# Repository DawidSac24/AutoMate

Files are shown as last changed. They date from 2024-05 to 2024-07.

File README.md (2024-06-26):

# AutoMate



> © INRACI


## Video 

https://github.com/DawidSac24/AutoMate/assets/171250080/86d8ad7e-6ad9-42c3-80ba-5ba671484344

## Summary

- [Project source](#Project-source)
- [Introduction](#Introduction)
- [The block diagram](#The-block-diagram) 
- [Characteristics](#Characteristics)
- [Used libraries](#Used-libraries)
- [My code](#My-code)
- [The principle diagrams](#The-principle-diagrams)
  - [The principle diagram without connector](#The-principle-diagram-without-connector)
  - [The principle diagram with connector](#The-principle-diagram-with-connector)
- [The PCB](#The-PCB) 
- [Parts list](#Parts-list) 
  - [XY table](#XY-table)
  - [Transmission](#Transmission)
  - [Electronics](#Electronics)
  - [Box](#Box)
  - [Bolting](#Bolting)

## Project source
I would like to sincerely thank the author of the site from which I drew inspiration :
[instructables.com/Automated-Chessboard](https://www.instructables.com/Automated-Chessboard/)

## Introduction
I am pleased to present my exciting project: Auto-Mate, an automated chess game designed to give a new dimension to this game. By enabling remote movement of pieces, I create the possibility of bringing chess online or against a robot on a chessboard. To achieve this, I have developed a case that handles the movement of the pieces. Auto-Mate is equipped with a screen, allowing for the automatic movement of pieces. It is also possible to move them manually using sensors located beneath the board. I made this project because I enjoy playing chess. It has allowed me to learn many new things in electronics and programming. Auto-mate is still in developpement (mostly the code). I invite you to see my work in the [TFE](TFE) folder, there is a more detailed documentation of my project. I also want to add that I am still a young student. My work and my code are far from perfect and contain many errors. My goal, above all, is to present my work and maybe inspire some people.

## The block diagram

Schema bloc

#### The Microcontroller
It is the brain of the setup, allowing control of each component (motors, motor drivers, electromagnet, multiplexers, and touchscreen) and reading the necessary data (limit switches, buttons, magnetic sensors, and touchscreen).
#### The Touchscreen
It provides the ability to navigate through menus to change the AI difficulty, display the timer, modify game settings, or select the game mode. It communicates with the UART, an asynchronous serial bus.
#### Motor Drivers A and B
They control the coils of the stepper motors and provide the necessary current to operate them.
#### Motors A and B
They are connected to a belt system, moving the electromagnet on the x and y axes.
#### The Electromagnet
It is placed underneath the board and is used to move the magnetized pieces on the board.
#### The Multiplexer
It successively reads the signals from the 8 sensors and sends the data to the microprocessor.
#### Magnetic Sensors
They determine the presence of the chess pieces.
#### x and y Limit Switches
They locate the position of the electromagnet by resetting at the start of the game. They allow for calibration of its position and help avoid potential misalignments during movement.

## Characteristics
### General :
- Color graphical resistive touchscreen, 320×240 pixels
- 2 arcade buttons
- 32 magnetized pieces
- Operating modes: 1/2 players
- Automatic piece movement
- Automatic piece detection
- Area for eliminated pieces
### Electronics :
- Power supply: 12V, 2A
### Mechanics :
- Dimensions: 496 mm x 496 mm x 100 mm
- 6 plywood faces
- Weight: 4 kg

## Used libraries
I planned to use a [Nextion library](https://docs.arduino.cc/learn/built-in-libraries/software-serial/) for the code of my touchscreen, but I accidentally connected my screen to the wrong pins of my microcontroller and had to use my touchscreen manually with the [SoftwareSerial library](https://docs.arduino.cc/learn/built-in-libraries/software-serial/).

## My code
I wanted to add an algorithm that would be used for an enemy robot. Unfortunately, I did not finish verifying the allowed moves for the pawns, which is required for the algorithm. If you would like to see my algorithm development then, you would have to wait for the next updates. To compensate, here is what I plan to do for the enemy robot algorithm:
obraz_2024-06-16_125101164

It is called the Min-Max algorithm, and I will use Alpha-Beta pruning, which evaluates unnecessary calculations and ignores unwanted possibilities. I invite you to search for some documentation about Min-Max and Alpha-Beta that is really interesting. Here is a video that explains the algorithm very well:
https://www.youtube.com/watch?v=l-hh51ncgDI&t=48s

## The principle diagrams
[easyEDA](https://oshwlab.com/ivaninraci/auto-mate)
### The principle diagram without connector
(https://oshwlab.com/ivaninraci/auto-mate)
### The principle diagram with connector
(https://oshwlab.com/ivaninraci/auto-mate)
## The PCB
(https://oshwlab.com/ivaninraci/auto-mate)
(https://oshwlab.com/ivaninraci/auto-mate)

## Parts list
### XY table
- 2 x V slot 20x20 linear rail, Length = 375 mm
- 1 x V slot 20x20 linear rail, Length = 350 mm
- 1 x V slot 20x20 linear rail, Length = 315 mm
- 1 x V slot 20x20 linear rail, Length = 395 mm
- 10 x 90 degree Corner Bracket
### Transmission
- 2 x GT2 Pulley, 20 teeth, 5mm bore
- 8 x GT2 Toothless pulley
- 3.5m x GT2 Belt
### Electronics
- 1 x Arduino Nano
- 2 x Stepper Motor - Adafruit - Nema 17 size - 200 steps/rev, 12V 350mA
- 2 x Stepper Motor Driver Carrier - Pololu - A4988
- 1 x Nextion touchscreen - NX3224T024
- 1 x Electromagnet - 5Kg Holding Force
- 1 x Freewheeling diode - 1N4001
- 1 x Power Transistor - TIP 120
- 2 x Micro Limit switch roller
- 64 x Reed Switch - Dia 2 x 14.5 mm
- 1 x Resistor - 1K ohm
- 4 x MUX breakout - SparkFun - CD74HC4067
### Box
- 2 x plywood - 470 x 470 x 10 mm
- 2 x plywood - 450 x 85 x 10 mm
- 2 x plywood - 450 x 85 x 10 mm
### Bolting
- 8 x Mini V Wheel
- 4 x Aluminium Spacer - ID : 5mm - Height : 6mm
- 4 x Eccentric Spacer - M5
- 4 x Hex. Locking Nut - M5
- 4 x Thin Hex. Nut - M5
- 8 x Mini Precision Shim - OD : 8 mm - ID : 5 mm - Thickness : 1 mm
- 26 x T-Nuts - M5
- 14 x Hex. Socket Button Head Cap Screw - M5 x 8 mm
- 12 x Hex. Socket Button Head Cap Screw - M5 x 12 mm
- 2 x Hex. Socket Button Head Cap Screw - M5 x 35 mm
- 2 x Hex. Socket Button Head Cap Screw - M5 x 30 mm
- 2 x Hex. Socket Button Head Cap Screw - M5 x 25 mm
- 8 x Hex. Socket Button Head Cap Screw - M5 x 15 mm
- 4 x Slotted Head Screw - M2 x 15 mm
- 4 x Nut - M2
- 8 x Hex. Socket Head Cap Screw - M3 x 10 mm
- 1 x Hex. Socket Head Cap Screw - M4 x 15 mm
- 4 x Slotted Countersunk Head Screw - M5 x 20 mm
- 4 x Nut - M5

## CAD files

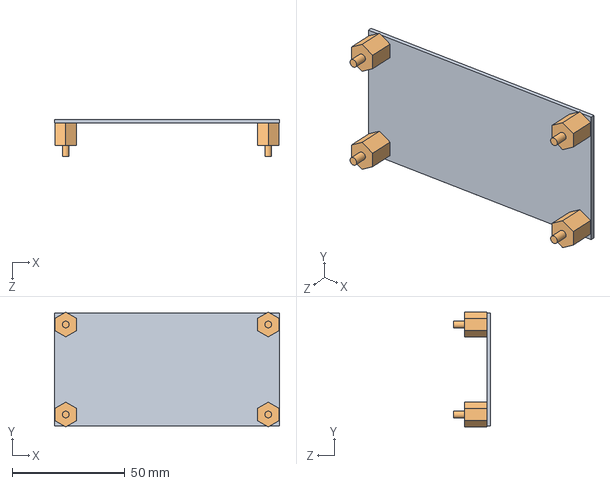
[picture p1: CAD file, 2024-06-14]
Technical drawings/PCB_Assemble.SLDASM
100.0 x 51.0 x 16.6 mm
PCB
Entretoise_1cm_Dawid x 4

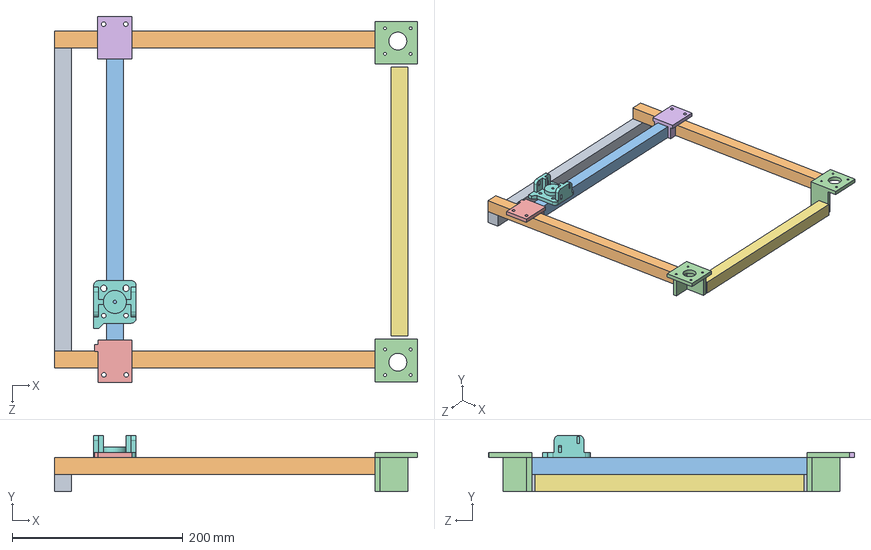
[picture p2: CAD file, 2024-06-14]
Technical drawings/Rails.SLDASM
425.0 x 66.0 x 429.0 mm
Rail_395
Rail_345 x 2
Rail_350
Support_moteur x 2
Support_milieu
Support_milieu_B
Rail_315
Support_aimant

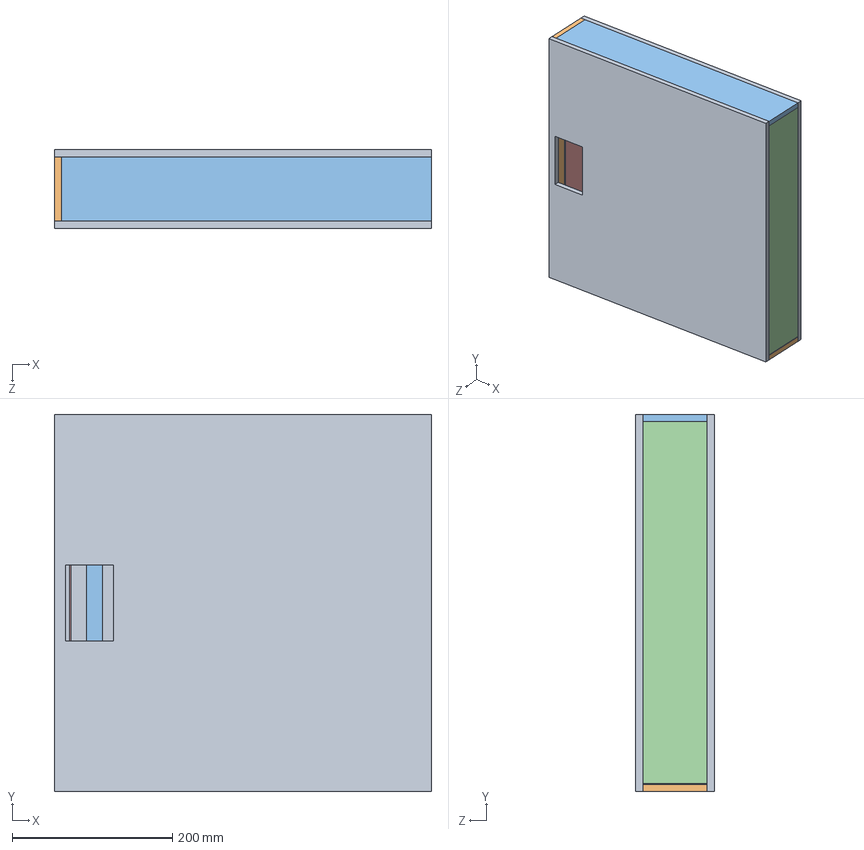
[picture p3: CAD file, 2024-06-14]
Technical drawings/Assamblage.SLDASM
470.0 x 470.0 x 98.0 mm
Face_Bas
Cote_Avant x 2
Cote_Arriere
Cote_droit
Rail_395
Rail_345 x 2
Rail_350
Support_moteur x 2
Support_milieu
Support_milieu_B
Rail_315
Support_aimant
PCB
Entretoise_1cm_Dawid x 4
pulley_support_A
pulley_support_B
Face_Haut

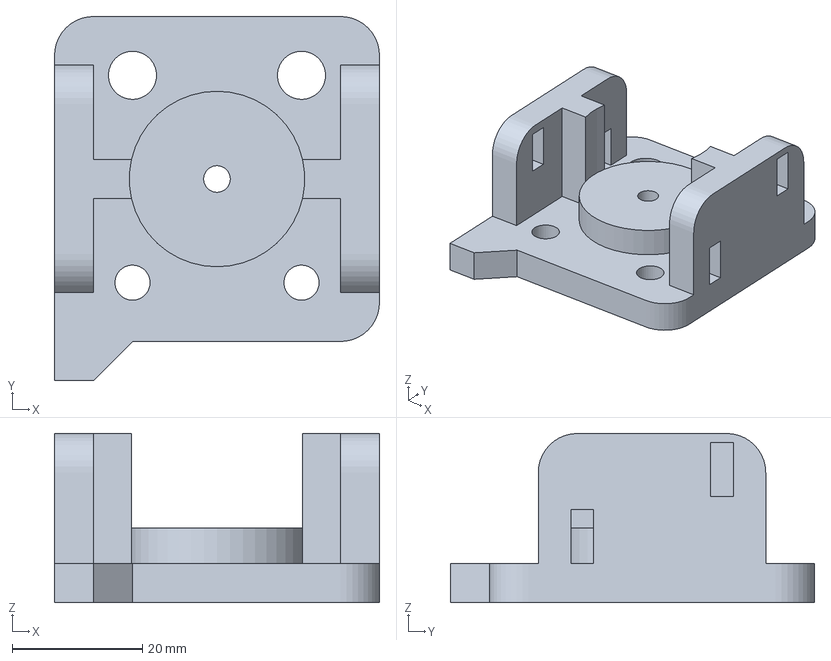
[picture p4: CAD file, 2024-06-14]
Technical drawings/Support_aimant.3mf
50.0 x 56.0 x 26.0 mm

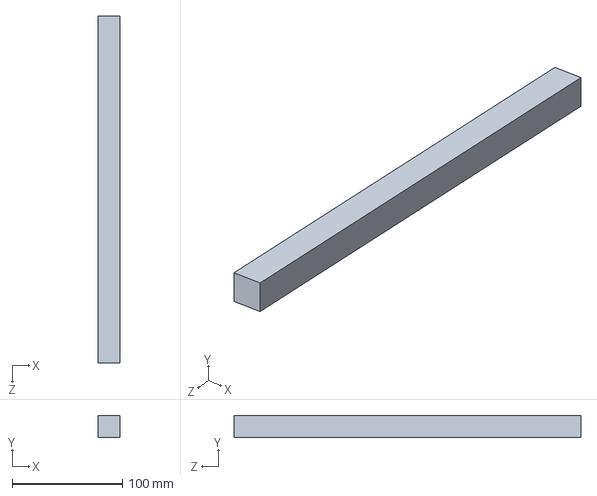
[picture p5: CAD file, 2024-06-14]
Technical drawings/V_Slot_Rails/Rail_315.SLDPRT
20.0 x 20.0 x 315.0 mm

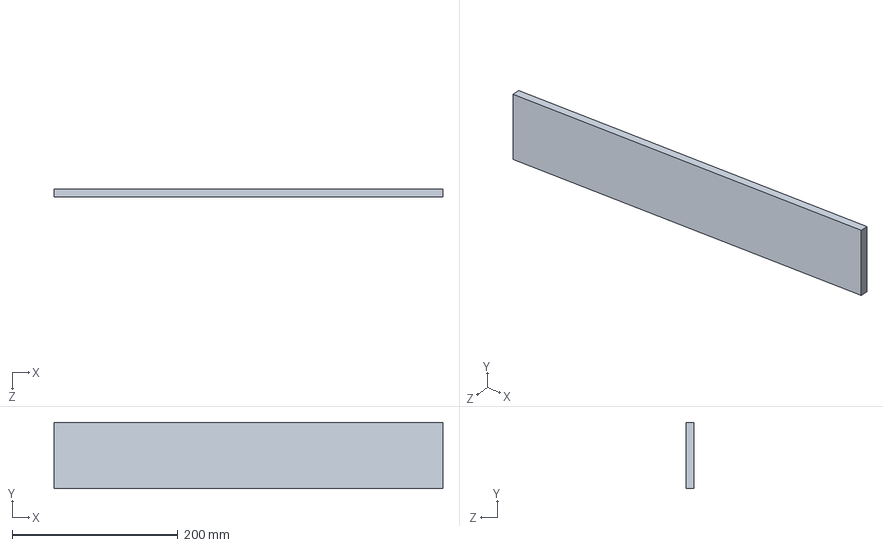
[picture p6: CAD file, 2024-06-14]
Technical drawings/Cote_Arriere.SLDPRT
470.0 x 80.0 x 10.0 mm

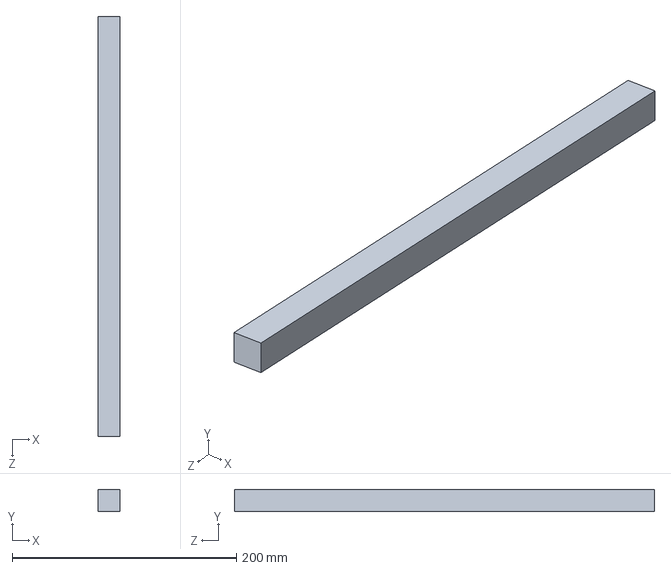
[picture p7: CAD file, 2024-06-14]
Technical drawings/V_Slot_Rails/Rail_345.SLDPRT
20.0 x 20.0 x 375.0 mm

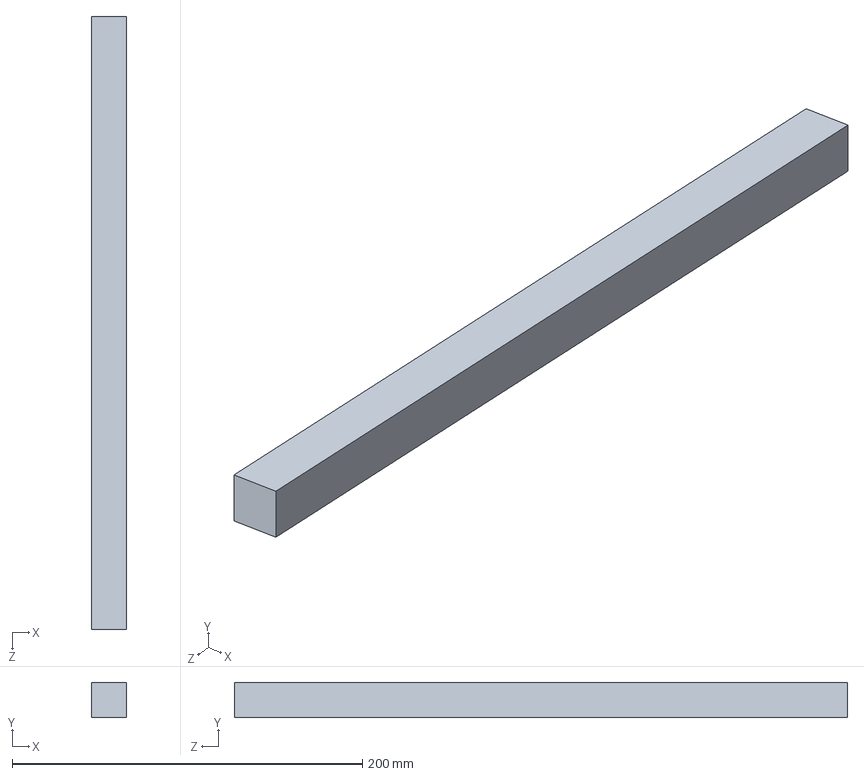
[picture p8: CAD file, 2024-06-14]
Technical drawings/V_Slot_Rails/Rail_350.SLDPRT
20.0 x 20.0 x 350.0 mm

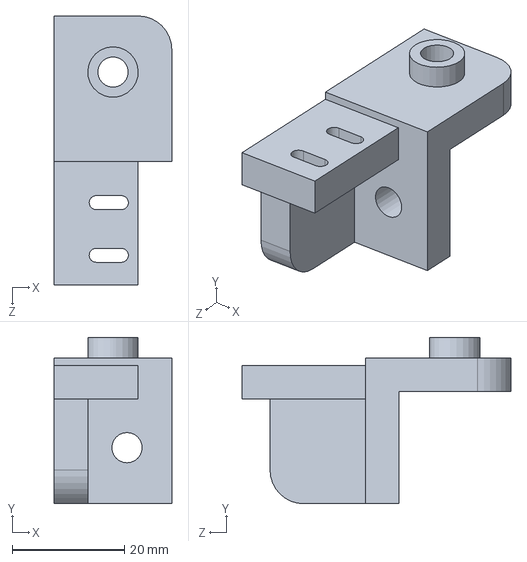
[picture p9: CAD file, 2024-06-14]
Technical drawings/pulley_support_A.SLDPRT
21.0 x 29.7 x 48.0 mm

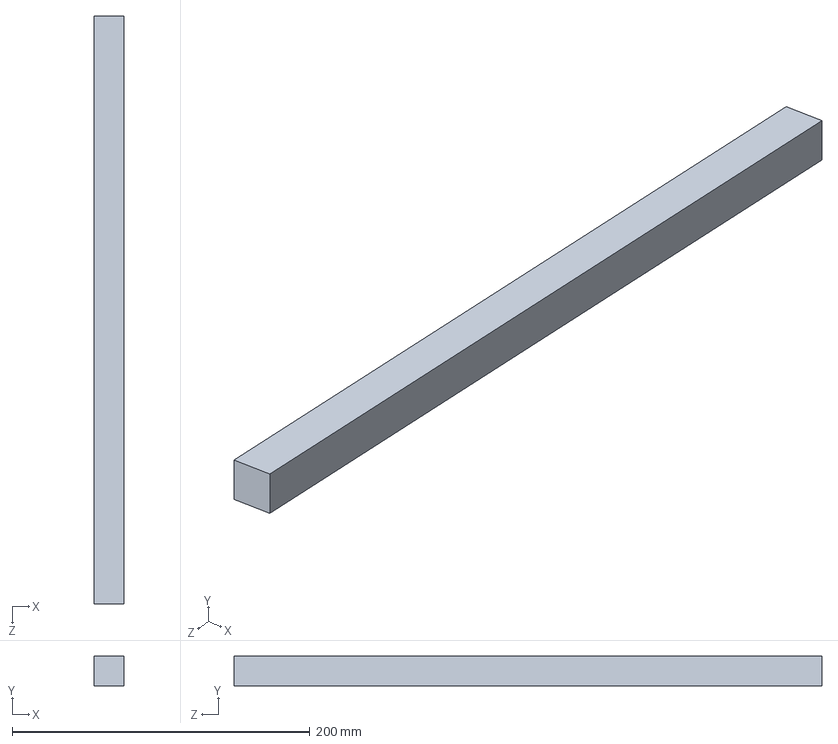
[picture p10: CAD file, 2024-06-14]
Technical drawings/V_Slot_Rails/Rail_395.SLDPRT
20.0 x 20.0 x 395.0 mm

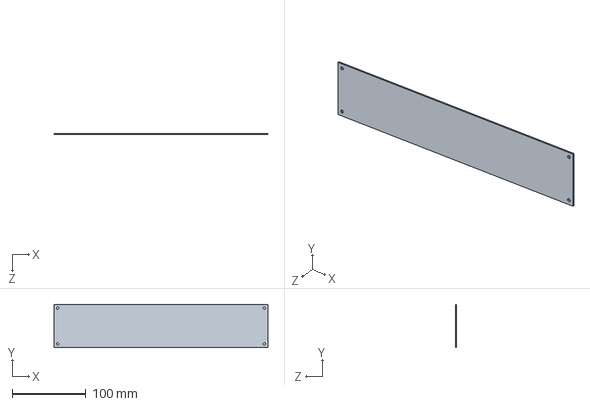
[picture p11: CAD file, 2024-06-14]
Technical drawings/PCB.SLDPRT
289.6 x 58.4 x 1.60 mm

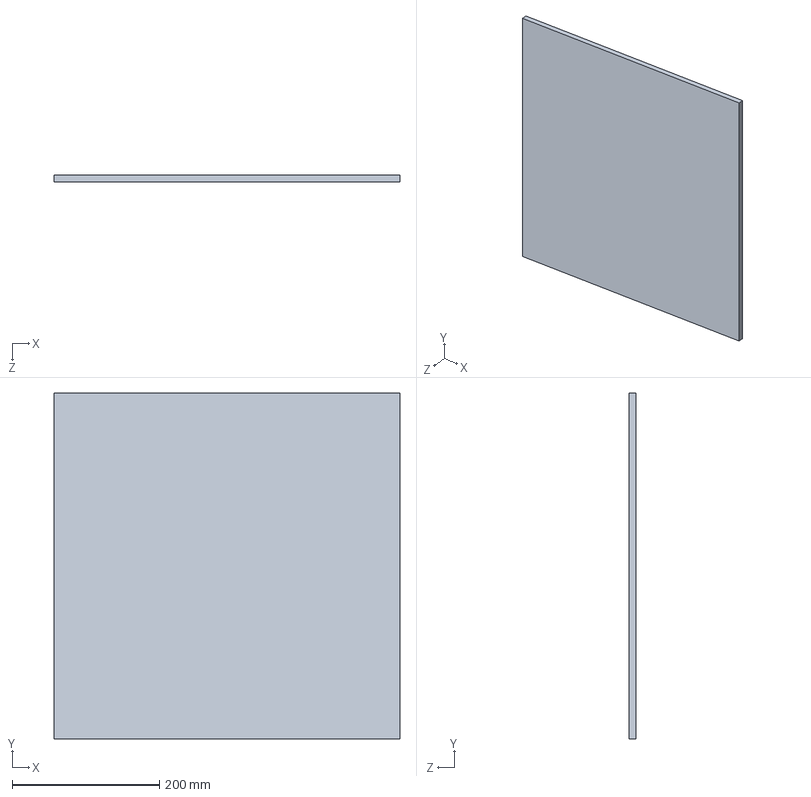
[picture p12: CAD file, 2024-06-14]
Technical drawings/Face_Bas.SLDPRT
470.0 x 470.0 x 10.0 mm

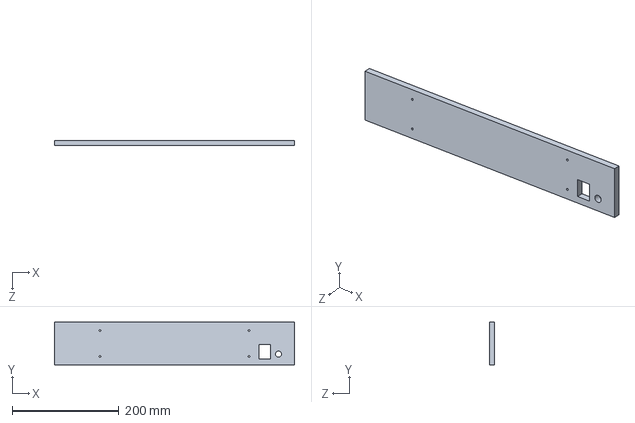
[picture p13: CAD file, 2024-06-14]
Technical drawings/Cote_Gauche.SLDPRT
450.0 x 80.0 x 10.0 mm

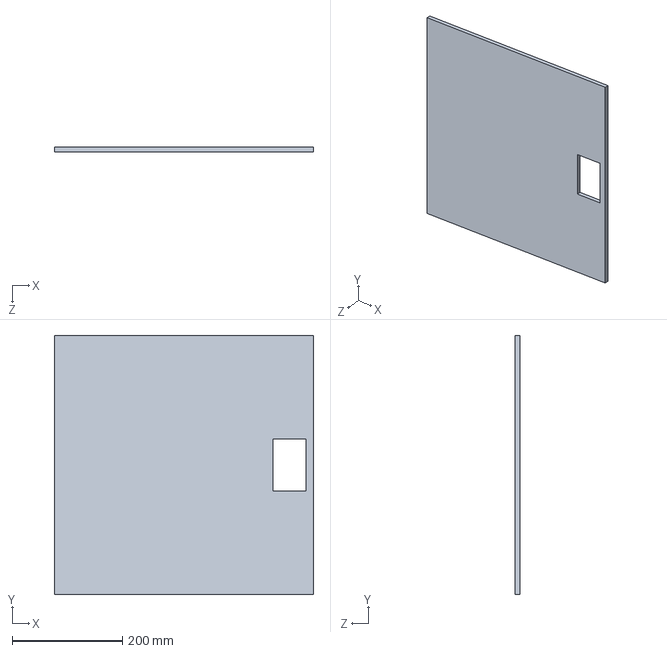
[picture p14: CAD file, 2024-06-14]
Technical drawings/Face_Haut.SLDPRT
470.0 x 470.0 x 9.00 mm

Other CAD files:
Technical drawings/Cote_Avant.SLDPRT
Technical drawings/Cote_droit.SLDPRT
Technical drawings/pulley_support_B.SLDPRT
Technical drawings/pulley_support_A.STL
Technical drawings/pulley_support_B.STL

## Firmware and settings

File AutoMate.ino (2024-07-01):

//  Automate_1.0.ino
//  Projet SIPS 2023-2024 : Auto-Mate
//  Sac Dawid 6ème éléctronique INRACI
/*  Hardware : Arduino Nano, moteur pas à pas Nema 17, driveur moteur - Pololu - A4988, éléctro-aimant, écran graphique Nextion
    transistor Darlington - TIP 120, capteurs à aimants, Multiplexeur - CD74HC4067, button d'arcade, fin de course  */
// 24.02.2024
//*****************************************************************************************************************************

//********************************************** LIBRAIRIES *******************************************************************
#include "global.h"
Dep dep();
//**********************************************************  VARIABLES GLOBALES *********************************************************************************
//******************************************* PLANCHE DE DEPART ***************************************************************
const int planche_depart[8][8] = {
  { TOUR_B, CHEVAL_B, FOU_B, DAME_B, ROI_B, FOU_B, CHEVAL_B, TOUR_B },
  { PION_B, PION_B, PION_B, PION_B, PION_B, PION_B, PION_B, PION_B },
  {},
  {},
  {},
  {},
  { PION_N, PION_N, PION_N, PION_N, PION_N, PION_N, PION_N, PION_N },
  { TOUR_N, CHEVAL_N, FOU_N, DAME_N, ROI_N, FOU_N, CHEVAL_N, TOUR_N },
};
//******************************************* PLANCHE  ************************************************************************
int planche[8][8];
int planche_precedent[8][8];
int pion_tempo;
//***************************** VARIABLES POUR LE DEPLACEMENT ************************************************************
int case_x[8] = { 0, 200, 400, 600, 800, 1000, 1200, 1400 };
int case_y[8] = { 1400, 1200, 1000, 800, 600, 400, 200, 0 };
int x_precedent;
int y_precedent;
int x_dep;
int y_dep;
int colonne_select;
int ligne_select;
int colonne_precedent;
int ligne_precedent;
bool pion_selectionne = false;
bool demonstration = false;

int vit_dep = 1000;  // milisecondesc
int nmbre_pas = 50;
int dir_moteur = 1;
int dir2;

int pos_x;
int pos_y;
//***************************** VARIABLES POUR Les multiplexeurs ************************************************************
int reed_sensor_status[8][8];
int reed_sensor_record[8][8];
int reed_sensor_status_memory[8][8];
const byte MUX_OUTPUT(12);
const byte MUX_ADDR[4] = { A3, A2, A1, A0 };  // A3 -> LSB A0 -> MSB
const byte MUX_SELECT[4] = { 9, 8, 7, 13 };

const byte MUX_CHANNEL[16][4] = {
  { 0, 0, 0, 0 },
  { 1, 0, 0, 0 },
  { 0, 1, 0, 0 },
  { 1, 1, 0, 0 },
  { 0, 0, 1, 0 },
  { 1, 0, 1, 0 },
  { 0, 1, 1, 0 },
  { 1, 1, 1, 0 },
  { 0, 0, 0, 1 },
  { 1, 0, 0, 1 },
  { 0, 1, 0, 1 },
  { 1, 1, 0, 1 },
  { 0, 0, 1, 1 },
  { 1, 0, 1, 1 },
  { 0, 1, 1, 1 },
  { 1, 1, 1, 1 }
};
//***************************** VARIABLES POUR LE MENU ************************************************************
int data[7];  // Déclaration d'un tableau d'entier
byte sequance;
int i;
int x = 100;
int page;
int id_bouton;
byte difficulty = 0;  // 0 => difficulté = facile
bool joueur_vs_joeur = true;
byte j1_choix_pion;  // si j1_choix_pion = 0 => couleur des pions du J1  = pas definie ; si 1 => couleur = blancs ; si 2 => couleur = noir
String nom_variable;
String information;
//***************************** VARIABLES POUR L'ETAT DE LA PARTIE ************************************************************
bool tour_blanc = true;
byte tour = 0;
//***************************** VARIABLES POUR LE TIMER ************************************************************
int timer_select = 3;
unsigned long t;
int minutes_blanc = 10;
int secondes_blanc = 1;
int minutes_noir = 10;
int secondes_noir = 1;
int minutes = 10;
int secondes = 1;
//***************************** VARIABLES AUTRES************************************************************
int sigval;
SoftwareSerial mySerial = SoftwareSerial(RXPIN, TXPIN);

//******************************************************************************************************************************
void setup() {
  Serial.begin(9600);    //   Initialise the Serial port at 2400 baud.
  mySerial.begin(9600);  //   Initialise the mySerial object at 9600 baud rate.
  pinMode(RXPIN, INPUT);
  pinMode(TXPIN, OUTPUT);

  pinMode(AIMANT, OUTPUT);

  pinMode(SIG, INPUT_PULLUP);
  pinMode(EN1, OUTPUT);
  digitalWrite(EN1, 0);

  while (!Serial) {}
  for (byte i = 0; i < 4; i++) {  // INITIALISATION des multiplexeurs
    pinMode(MUX_ADDR[i], OUTPUT);
    digitalWrite(MUX_ADDR[i], LOW);
    pinMode(MUX_SELECT[i], OUTPUT);
    digitalWrite(MUX_SELECT[i], HIGH);
  }
  pinMode(MUX_OUTPUT, INPUT_PULLUP);
  for (byte i = 2; i < 6; i++) {
    for (byte j = 0; j < 8; j++) {
      reed_sensor_status[i][j] = 1;
      reed_sensor_status_memory[i][j] = 1;
    }
  }
  
  dep.init();

  Serial.println("ready to start");
  t = millis;
}

void loop() {
  if (mySerial.available() > 0) {
    for (i = 0; i < 7; i++) {
      data[i] = mySerial.read();
      Serial.println(data[i]);
    }
    page = data[1];
    id_bouton = data[2];
    switch (page) {
      //**********************************************************  PAGE : Menu principal *********************************************************************************
      case 0:
        if (id_bouton == 1) {  // Appui du bouton PLAY
          demarrage_partie();
        }
        break;
      //**********************************************************  PAGE : Menu principal *********************************************************************************
      case 1:
        if (id_bouton == 2)
          dep.demo();
        break;
      //**********************************************************  PAGE : Choix de la difficulté de la partie ************************************************************
      case 3:
        switch (id_bouton) {
          case 4:
            if (difficulty < HARD)
              difficulty++;
            break;
          case 8:
            if (difficulty > EASY)
              difficulty--;
            break;
        }
        Serial.print("difficulté = ");
        Serial.println(difficulty);
        break;
      //**********************************************************  PAGE : Choix du temps de la partie ********************************************************************
      case 4:
        switch (id_bouton) {
          case 4:
            if (timer_select < 5)
              timer_select++;
            Serial.println(timer_select);
            break;
          case 7:
            if (timer_select > 1)
              timer_select--;
            Serial.println(timer_select);
            break;
        }
        break;
      //**********************************************************  PAGE : Choix de la couleur de pion ********************************************************************
      case 5:
        switch (id_bouton) {
          case 1:  // CHOIX DE COULEUR DE PION : Blanc
            j1_choix_pion = 1;
            break;
          case 2:  // CHOIX DE COULEUR DE PION : Noire
            j1_choix_pion = 2;
            break;
          case 3:  // CHOIX DE COULEUR DE PION : Aleatoire
            j1_choix_pion = random(1, 3);
            break;
        }
        Serial.print("Tour du joueur 1 = ");
        Serial.println(j1_choix_pion);
        break;
      //**********************************************************  PAGE : Debug ******************************************************************************************
      case 6:
        Serial.println("Page Debug");
        dep.reset();
        ligne_select = 7;
        colonne_select = 0;
        x_precedent = 0;
        y_precedent = 0;
        break;
      //**********************************************************  PAGE : Play, choix de ligne ***************************************************************************
      case 8:
        if (id_bouton == 10 || id_bouton == 11) {
        }  // bouton actionné : retour OU paramètres
        else {
          Serial.print("ligne = ");
          ligne_select = id_bouton - 2;
          Serial.println(ligne_select);
          calibrate();
        }
        break;
      //**********************************************************  PAGE : Play, choix de colonne *************************************************************************
      case 9:
        if (id_bouton > 1 && id_bouton < 10) {  // un des boutons pour le choix de la colonne à été actionné
          if (tour >= 1) {
            tour_blanc = !tour_blanc;
            if (sequance == JOUEUR_BLANC)
              sequance = JOUEUR_NOIR;
            else
              sequance = JOUEUR_BLANC;
            tour = 0;
          } else
            tour++;

          Serial.print("tour ");
          Serial.println(tour);
          Serial.print("tour_blanc ");
          Serial.println(tour_blanc);

          calibrate();

          // Serial.print("colonne = ");
          colonne_select = id_bouton - 2;
          // Serial.println(colonne_select);

          dep.pion();


        } else if (id_bouton == 11) {
        }                            // bouton actionné : paramètres
        else if (id_bouton == 14) {  // bouton actionné : retours
          tour--;
          calibrate();
        }
        break;
      //**********************************************************  PAGE : Paramètres durent la parie *********************************************************************
      case 10:
        if (data[2] == 1)
          calibrate();
        if (data[2] == 2) {
          dep.reset();
          x_precedent = 0;
          y_precedent = 0;
        }
        break;
    }
  }
  switch (sequance) {
    case JOUEUR_BLANC:
      if (millis() - t > 995) {  // Display the white player clock
        decompte();
        // Serial.println("JOUEUR_BLANC");
        nom_variable = "n0.val=";
        envoi_ecran_val(&nom_variable, &minutes_blanc);
        nom_variable = "n1.val=";
        envoi_ecran_val(&nom_variable, &secondes_blanc);
        affichage_planche();
        affichage_aimants();
      }
      break;

      break;
    case JOUEUR_NOIR:
      if (millis() - t > 995) {  // Display the black player clock
        decompte();
        // Serial.println("JOUEUR_NOIR");
        nom_variable = "n0.val=";
        envoi_ecran_val(&nom_variable, &minutes_noir);
        nom_variable = "n1.val=";
        envoi_ecran_val(&nom_variable, &secondes_noir);
        affichage_planche();
        affichage_aimants();
      }
      break;
  }
}

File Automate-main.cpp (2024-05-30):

#include "Automate.h"

void dep_horizontal(int *temps, int *pas, int *dir) {  // dir 1 = gauche et dir 2 = droite
  digitalWrite(DIR1, *dir);
  digitalWrite(DIR2, *dir);
  for (int x = 0; x < *pas; x++) {
    digitalWrite(STEP1, 1);
    digitalWrite(STEP2, 1);
    delayMicroseconds(*temps);
    digitalWrite(STEP1, 0);
    digitalWrite(STEP2, 0);
    delayMicroseconds(*temps);
  }
}

void dep_vertical(int *temps, int *pas, int *dir) {  // dir 1 = haut dir 2 = bas
  if (*dir == 1) {
    digitalWrite(DIR1, !*dir);
    digitalWrite(DIR2, *dir);
  } else {
    digitalWrite(DIR1, *dir);
    digitalWrite(DIR2, !*dir);
  }
  for (int x = 0; x < *pas; x++) {
    digitalWrite(STEP1, 1);
    digitalWrite(STEP2, 1);
    delayMicroseconds(*temps);

    digitalWrite(STEP1, 0);
    digitalWrite(STEP2, 0);
    delayMicroseconds(*temps);
  }
}

void envoi_ecran() {
  mySerial.write(0xff);  // We always have to send this three lines after each command sent to the nextion display.
  mySerial.write(0xff);
  mySerial.write(0xff);
}

void reset_pos() {
  // dep vers l'arriere
  vit_dep = 1800;

  nmbre_pas = 50;
  dir_moteur = 1;
  dep_vertical(&vit_dep, &nmbre_pas, &dir_moteur);

  // dep vers la gauche
  nmbre_pas = 80;
  dep_horizontal(&vit_dep, &nmbre_pas, 1);

  // aimant va vers l'avant
  dir_moteur = 2;
  digitalWrite(DIR1, dir_moteur);
  digitalWrite(DIR2, !dir_moteur);
  while (digitalRead(FCA)) {
    digitalWrite(STEP1, 1);
    digitalWrite(STEP2, 1);
    delayMicroseconds(vit_dep);
    digitalWrite(STEP1, 0);
    digitalWrite(STEP2, 0);
    delayMicroseconds(vit_dep);
  }

  // aimant va a droite
  dir_moteur = 2;
  digitalWrite(DIR1, dir_moteur);
  digitalWrite(DIR2, dir_moteur);
  while (digitalRead(FCB)) {
    digitalWrite(STEP1, 1);
    digitalWrite(STEP2, 1);
    delayMicroseconds(vit_dep);

    digitalWrite(STEP1, 0);
    digitalWrite(STEP2, 0);
    delayMicroseconds(vit_dep);
  }
  nmbre_pas = 50;  //                              deplacement vers la case H1
  dir_moteur = 1;
  dep_vertical(&vit_dep, &nmbre_pas, &dir_moteur);
  nmbre_pas = 40;
  dep_horizontal(&vit_dep, &nmbre_pas, 2);
}

void decompte() {  //
  //  Set the time of the current player
  if (tour == 2) {
    tour = 0;
    if (sequance == JOUEUR_BLANC) {
      minutes = secondes_blanc;
      minutes = minutes_blanc;
    } else if (sequance == JOUEUR_NOIR) {
      secondes = secondes_noir;
      minutes = minutes_noir;
    }
  }

  t = millis();
  // Serial.println(secondes);
  secondes--;
  if (secondes <= 0) {
    minutes--;
    secondes = 60;
  }
  // Serial.println(minutes);

  //  Record the white player time
  if (sequance == JOUEUR_BLANC) {
    secondes_blanc = secondes;
    minutes_blanc = minutes;
  }
  //  Record the black player time
  else if (sequance == JOUEUR_NOIR) {
    secondes_noir = secondes;
    minutes_noir = minutes;
  }
}

void calibrate() {

  Serial.println("sequance = CALIBRATE");

  if (tour_blanc == true) {
    mySerial.print("n0.val=");  // envoi des minutes et secondes ==> calibrer le 2 decomptes (Arduino et Nextion)
    mySerial.print(minutes_blanc);
    envoi_ecran();
    mySerial.print("n1.val=");
    mySerial.print(secondes_blanc);
    envoi_ecran();

    mySerial.print("t0.txt=");  // envoi des minutes et secondes ==> calibrer le 2 decomptes (Arduino et Nextion)
    mySerial.print("\"");
    mySerial.print("WHITE'S TURN");
    mySerial.print("\"");
    envoi_ecran();
    joueur_blanc();
  } else {
    mySerial.print("n0.val=");  // envoi des minutes et secondes ==> calibrer le 2 decomptes (Arduino et Nextion)
    mySerial.print(minutes_noir);
    envoi_ecran();
    mySerial.print("n1.val=");
    mySerial.print(secondes_noir);
    envoi_ecran();

    mySerial.print("t0.txt=");  // envoi des minutes et secondes ==> calibrer le 2 decomptes (Arduino et Nextion)
    mySerial.print("\"");
    mySerial.print("BLACK'S TURN");
    mySerial.print("\"");
    envoi_ecran();
    joueur_noir();
  }
}

void demarrage_partie() {
  calibrate();

  reset_pos();
  Serial.println("sequance = START");

  switch (timer_select) {
    case 1:
      minutes_blanc = 3;
      minutes_noir = 3;
      break;
    case 2:
      minutes_blanc = 5;
      minutes_noir = 5;
      break;
    case 3:
      minutes_blanc = 10;
      minutes_noir = 10;
      break;
    case 4:
      minutes_blanc = 30;
      minutes_noir = 30;
      break;
    case 5:
      minutes_blanc = 60;
      minutes_noir = 60;
      break;
  }
  secondes = 0;
  secondes_blanc = 1;
  secondes_noir = 1;

  tour = 0;
  tour_blanc = true;
  case_choisie = false;
  pion_selectionne = false;
}

void joueur_blanc() {
  sequance = JOUEUR_BLANC;
  Serial.println("JOUEUR_BLANC");
  if (millis() - t > 995) {  // Display the white player clock
    decompte();
    mySerial.print("n0.val=");  // envoi des minutes et secondes ==> calibrer le 2 decomptes (Arduino et Nextion)
    mySerial.print(minutes_blanc);
    envoi_ecran();
    mySerial.print("n1.val=");
    mySerial.print(secondes_blanc);
    envoi_ecran();
  }
}

void joueur_noir() {
  sequance = JOUEUR_NOIR;
  Serial.println("JOUEUR_NOIR");
  if (millis() - t > 995) {  // Display the black player clock
    decompte();
    mySerial.print("n0.val=");  // envoi des minutes et secondes ==> calibrer le 2 decomptes (Arduino et Nextion)
    mySerial.print(minutes_noir);
    envoi_ecran();
    mySerial.print("n1.val=");
    mySerial.print(secondes_noir);
    envoi_ecran();
  }
}
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

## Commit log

2024-05-30 action debile de Mr Kapita
2024-05-30 correction des betises de mr Kapita
    [AutoMate.ino, Automate.cpp]
2024-05-30 creation de foncion envoi_ecran1
2024-06-02 Correction de la fonction envoi_ecran1
    [Automate.cpp]
2024-06-03 correction de envoi_ecran1() + correction du timer
    [AutoMate.ino, Automate.cpp]
2024-06-04 correction de du joueur (pas fini)
    [AutoMate.ino, Automate.cpp]
2024-06-04 correction du systeme de tours
    [AutoMate.ino]
2024-06-04 correction de demarrage_partie et nettoyage du programme
    [AutoMate.ino, Automate.cpp]
2024-06-06 changement de fichiers
2024-06-06 ajout de demo()
2024-06-11 modif de demo()
2024-06-12 ajout de la lecture des capteurs a aimants
2024-06-14 technical drawings file
    [Assamblage.SLDASM, Cote_Arriere.SLDPRT, Cote_Avant.SLDPRT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]
2024-07-01 creation de la classe dep
